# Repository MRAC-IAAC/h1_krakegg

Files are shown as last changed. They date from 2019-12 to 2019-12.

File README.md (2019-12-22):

# h1_krakegg

Krakegg is a soft robotics project exploring the implementation of bionic actuation for soft robotics grippers.

The repository contains the files, code & hardware components used in the project.

In the documents, you will find:

**A. Text instructions:**

0.Concept & process: explaining the overall process leading to the development of the final prototype for the soft robotics gripper.

0_01: Bill of materials: a list of the materials used for the production of the final prototype, with affiliated links to similar products that can be purchased from Amazon/ local retailers.

0_02: Build process: documenting the steps taken in order to build the final prototype

**B. 3D printing files:**

Structure : Print files for the air chamber, exoskeleton, and connection to the robot

Moulds : Print file for the silicone moulds for the fingers and knuckle spacer

**C. Circuit:**

03_circuit: Circuit diagrams for the communication and control circuit

03_arduino: Arduino code for the air control circuit

**Prototype demonstration videos:**

    Egg picking demonstration: https://www.youtube.com/watch?v=kh5d-S89E1A&feature=youtu.be

    Force sensor test: https://www.youtube.com/watch?v=OoQZakSipXg&feature=emb_title

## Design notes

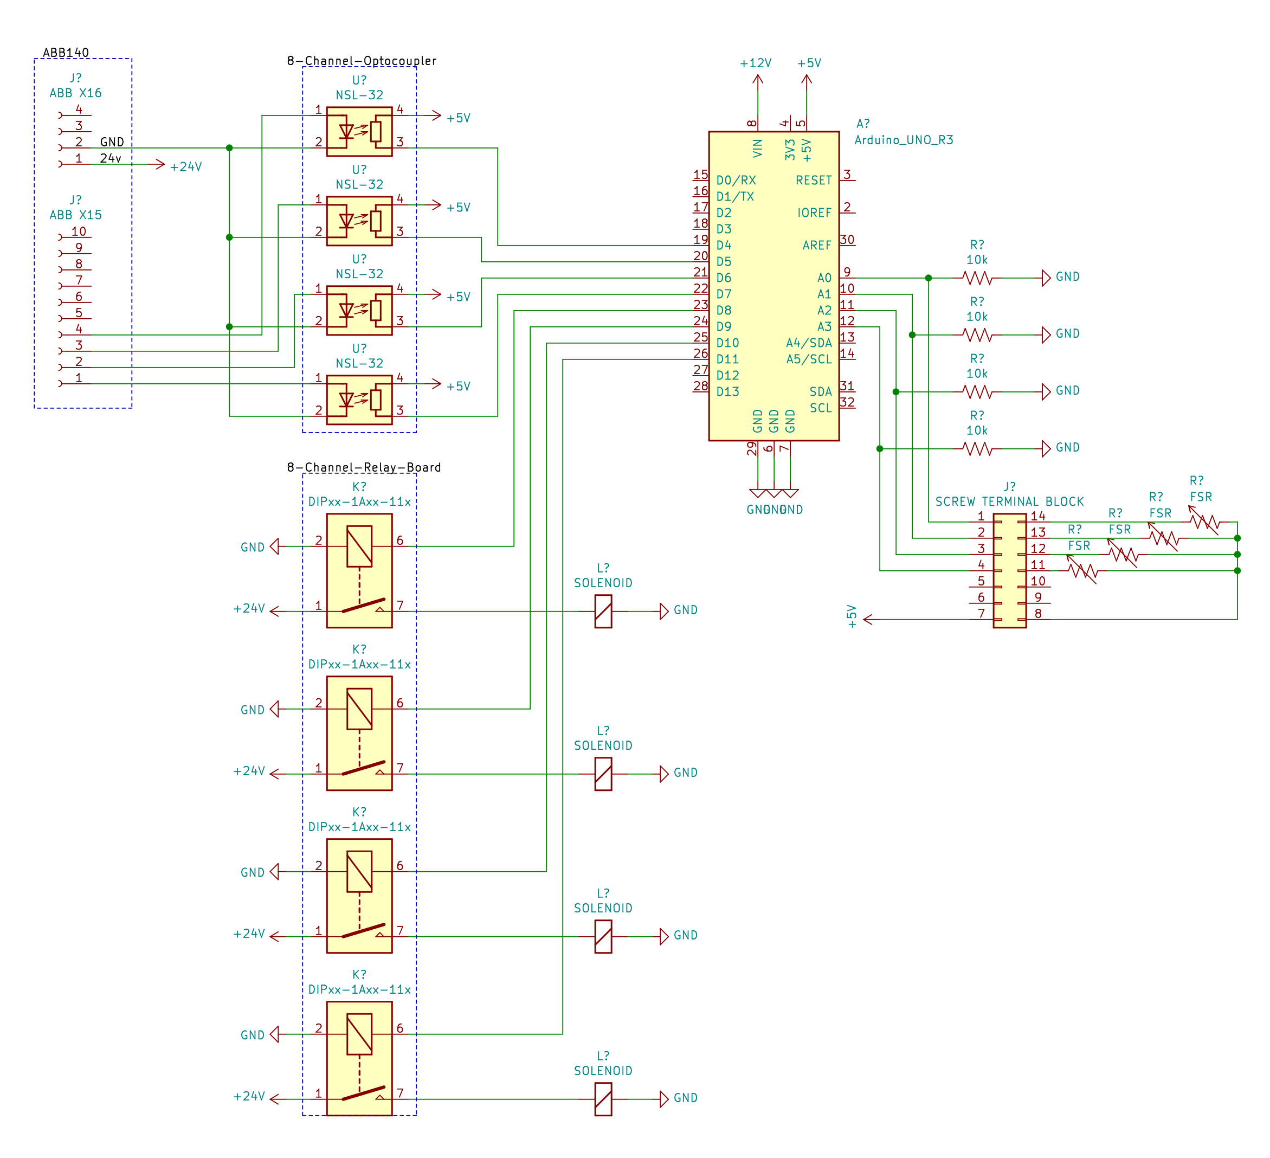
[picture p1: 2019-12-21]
images/soft-gripper-schematic.png

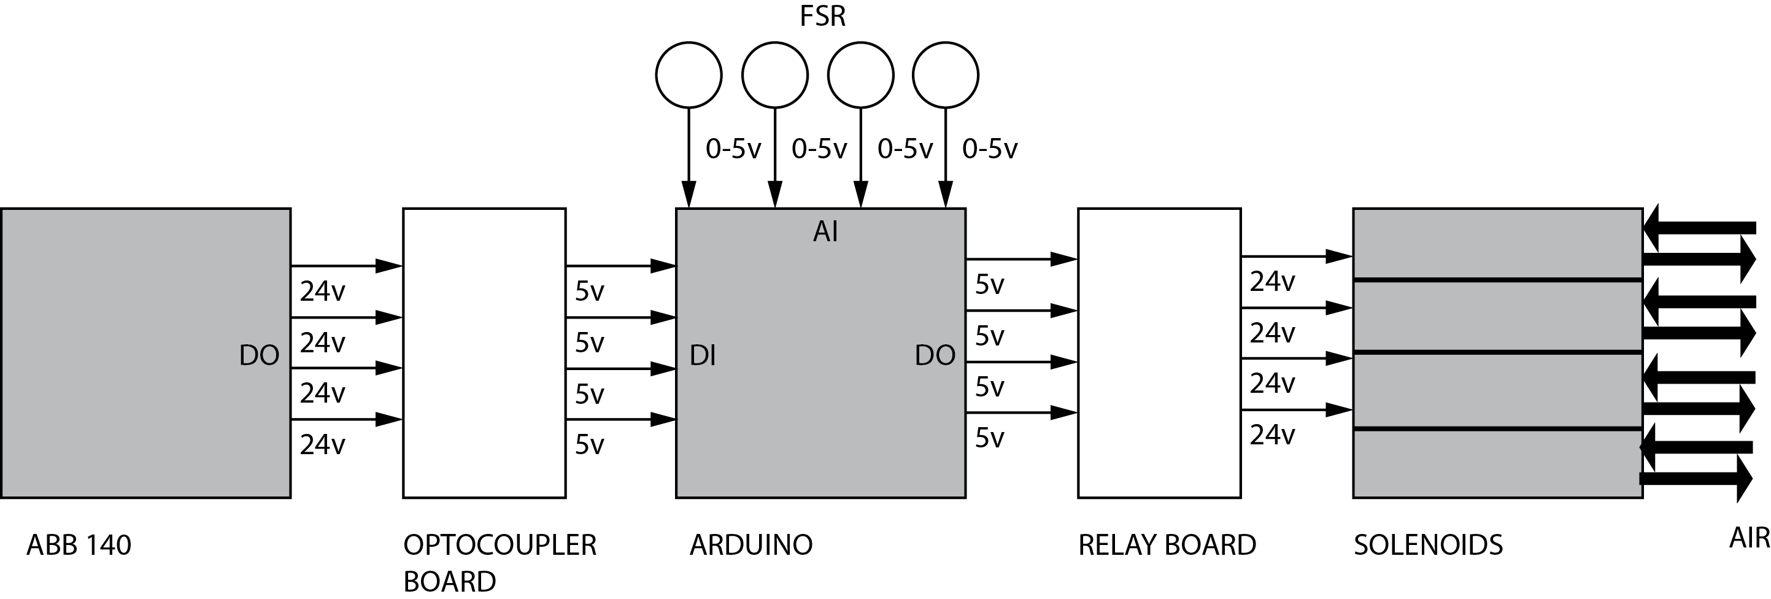
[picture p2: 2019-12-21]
images/gripper_board_diagram.png

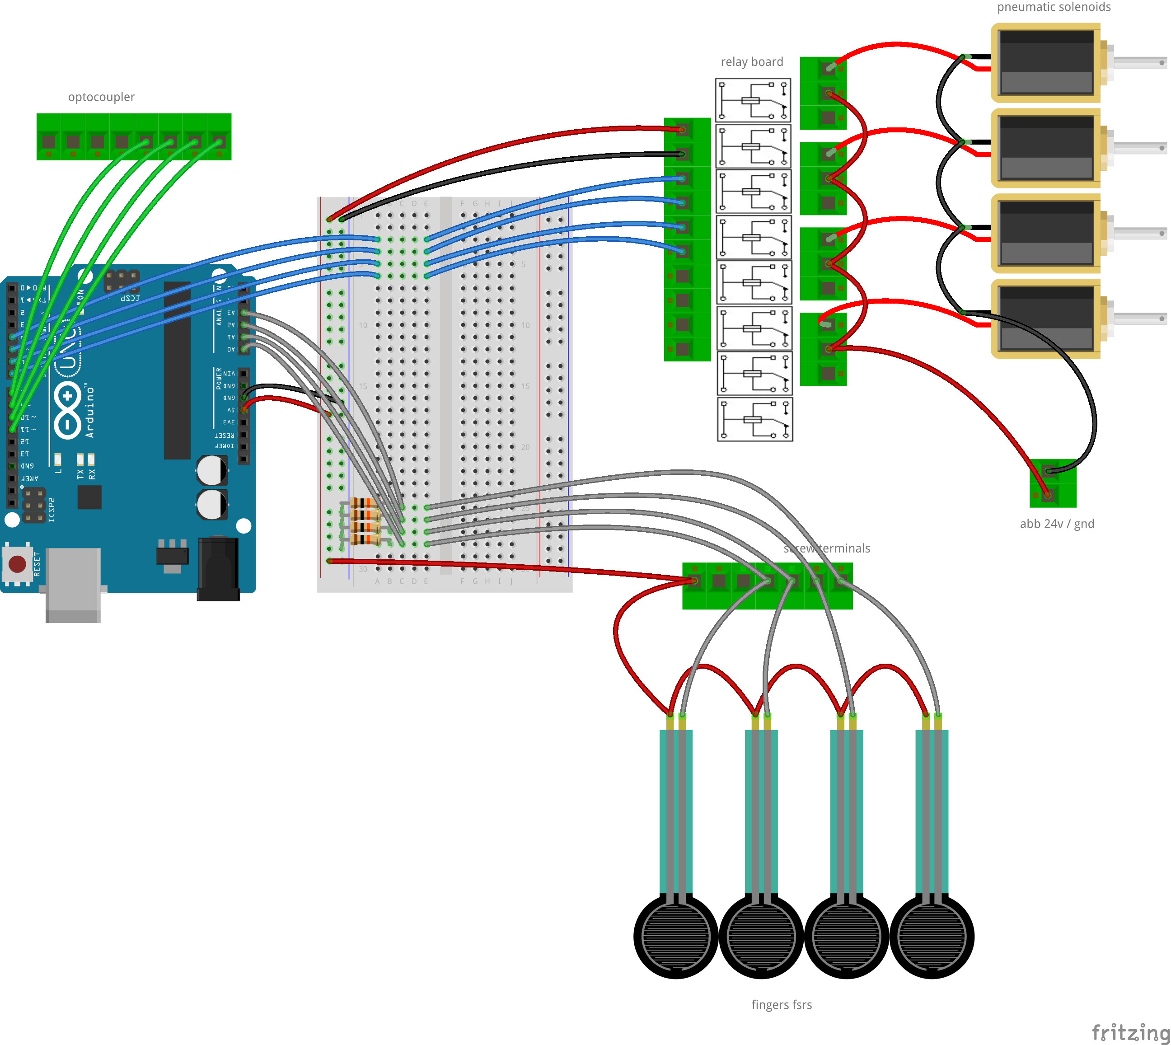
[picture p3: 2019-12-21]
images/soft_gripper_board_layout_bb.png

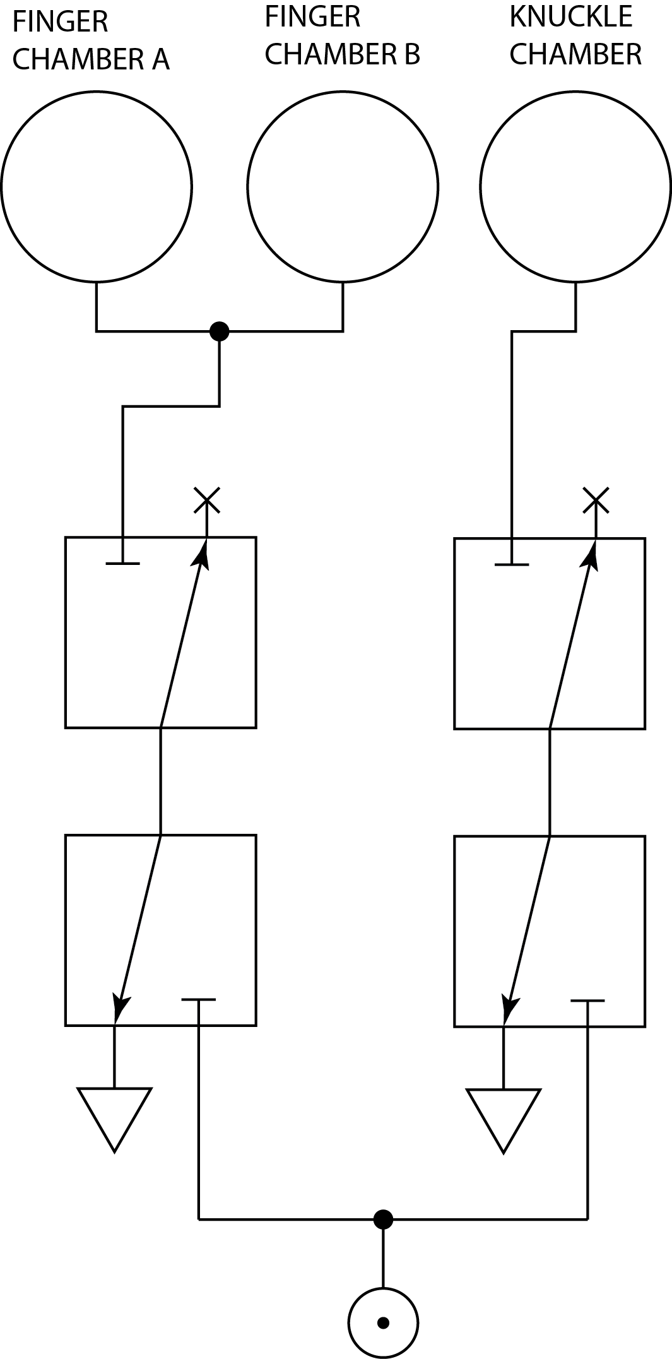
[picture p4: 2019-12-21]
images/pneumatic-diagram.png

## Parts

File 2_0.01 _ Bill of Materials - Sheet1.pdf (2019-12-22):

Bill of Materials

Printing and Casting
Item | Count | Purchase
PLA Printer Filament | 1 | https://www.amazon.com/OVERTURE-Filament-Consumables-Dimensional-Accuracy/dp/B07PGZNM34/
Casting Silicone | ~0.5 lbs | https://www.amazon.com/Smooth-Ecoflex-00-50-Platinum-Silicone/dp/B00GJ80HIC

Connections
Item | Count | Purchase
M3,M5 Bolts | | https://www.amazon.com/Hilitchi-510pcs-Stainless-Socket-Assortment/dp/B073SW4S6C
Pop Rivets | 4 | https://www.amazon.com/Tradespro-836341-Aluminum-Assortment-500-Piece/dp/B003L116P8

Electronics
Item | Count | Purchase
12v Power Supply | 1 | https://www.amazon.com/Switching-Universal-Regulated-Transformer-Computer/dp/B07C2WBR1L
Arduino Uno R3 Microcontroller | 1 | https://www.amazon.com/RoboGets-Compatible-ATmega328P-Microcontroller-Electronics/dp/B01N4LP86I
Optocoupler Board (4+ Channels) | 1 | https://www.amazon.com/24V-Optocoupler-Voltage-Level-Converter/dp/B06XKSFGXX
Relay Board (4+ Channels) | 1 | https://www.amazon.com/ELEGOO-Channel-Optocoupler-Arduino-Raspberry/dp/B01HCFJC0Y/
Force Sensitive Resistors | 4 | https://www.amazon.com/Sensitive-Resistor-Pressure-Diameter-Resistance-Type/dp/B07MP4RL9Q
Breadboard or Protoboard | 1 | https://www.amazon.es/Protoboard-contactos-Breadboard-prototipos-soldadura/dp/B00JGFDKBQ
10k Resistors | 4 | https://www.taydaelectronics.com/10-x-resistor-10k-ohm-1-4w-5-carbon-film-pkg-of-10.html
Mounting Plate or Project Box | 1
Jumper Cables and Wires | | https://www.amazon.com/Elegoo-EL-CP-004-Multicolored-Breadboard-arduino/dp/B01EV70C78
Screw Terminal Block (8 Positions) | 1 | https://www.amazon.com/a10073000ux0031-Position-Terminal-Covered-Barrier/dp/B00UWVYA30/

Pneumatics
Item | Count | Purchase
3 Way 2 Position 24 Pneumatic Solenoid | 4 | https://www.amazon.com/Position-Pneumatic-Electric-Solenoid-Valve/dp/B07YXSWZF4
Air Compressor | 1 | https://www.amazon.com/AstroAI-Portable-Compressor-Inflator-Protection/dp/B078LYX5YF
6mm Pneumatic Tubing | ~6m | https://www.amazon.com/uxcell-Pneumatic-Polyurethane-Meter-32-8ft/dp/B07859JVCY
6mm Pneumatic Push Connectors | 12 | https://www.amazon.com/Thread-Straight-Pneumatic-Fitting-Connectors/dp/B07BLRG8SH
6mm Pneumatic Splitter | 2 | https://www.amazon.com/Sydien-Connect-Pneumatic-Fittings-Splitter/dp/B07H14PVW2/

Tools
Item
Syringe
Soldering Iron
Wire STrippers
Tweezers
Screwdriver
Allen Wrenches
3d Printer

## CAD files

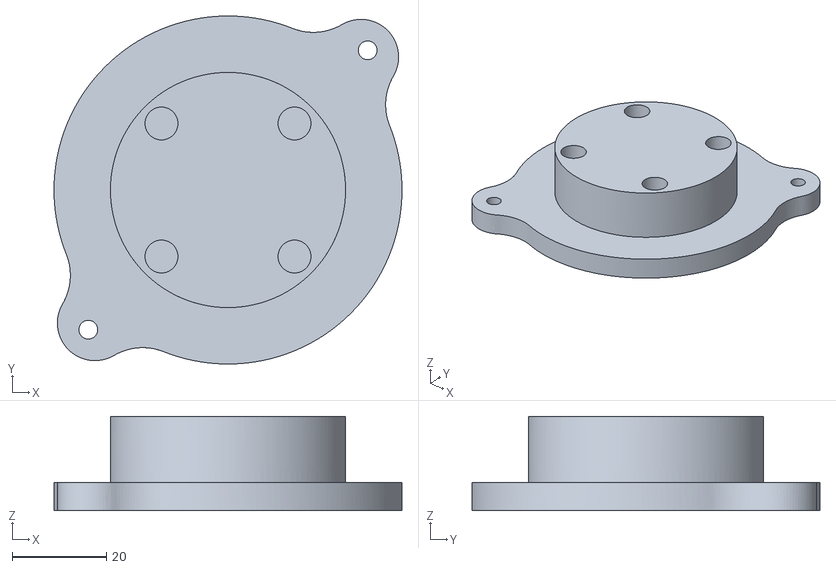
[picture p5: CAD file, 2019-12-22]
print_files/structure_connection_plane.stl
74.0 x 74.0 x 20.0

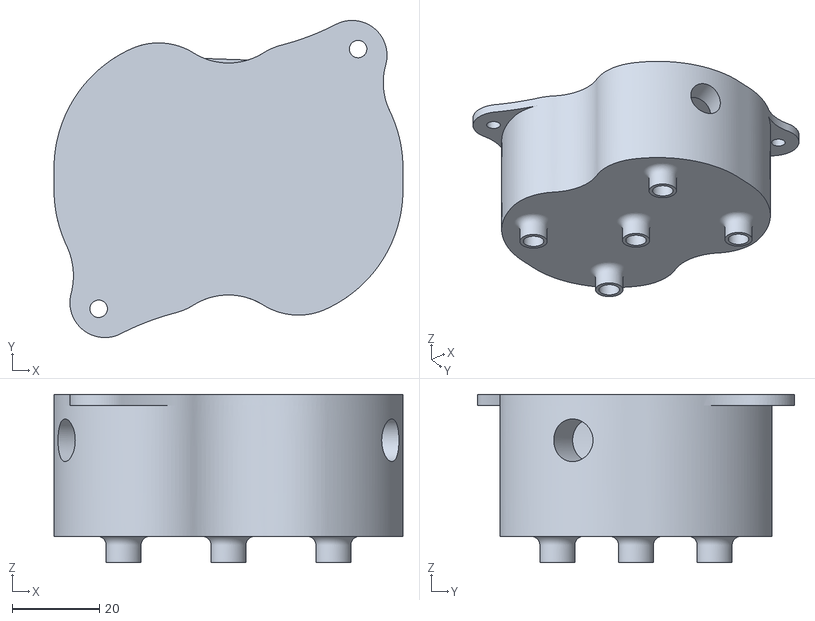
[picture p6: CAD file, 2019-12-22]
print_files/structure_air_chamber.stl
79.9 x 72.6 x 38.5

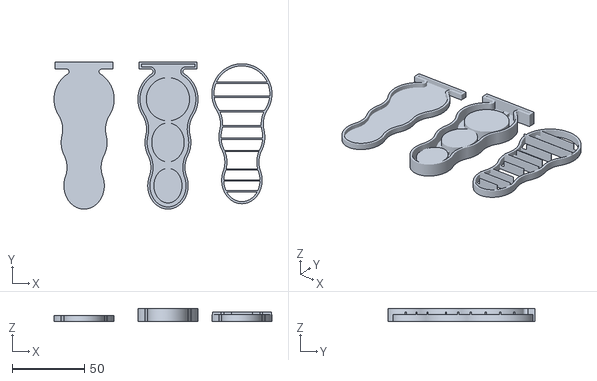
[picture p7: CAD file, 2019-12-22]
print_files/mould-fingers.stl
151.4 x 102.2 x 9.00

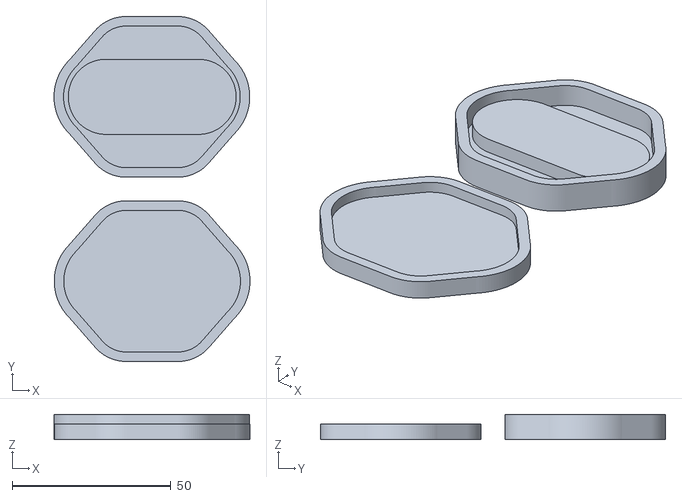
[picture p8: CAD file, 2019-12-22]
print_files/mould_knuckle_01.stl
61.7 x 108.7 x 8.00

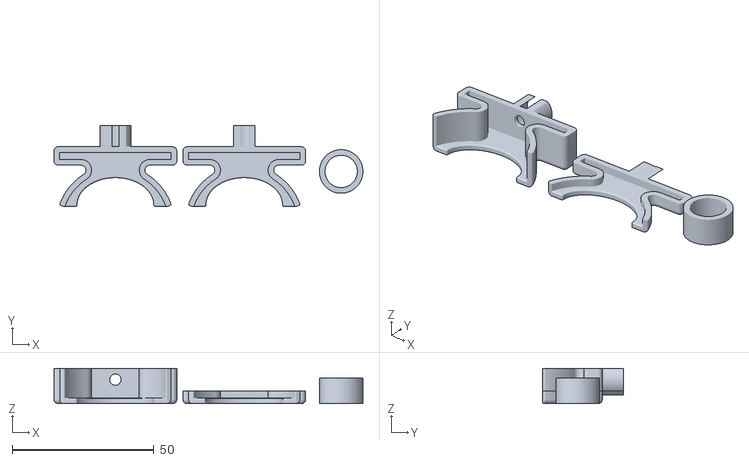
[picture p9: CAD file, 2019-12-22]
print_files/structure_exoskeleton.stl
109.0 x 28.6 x 12.5

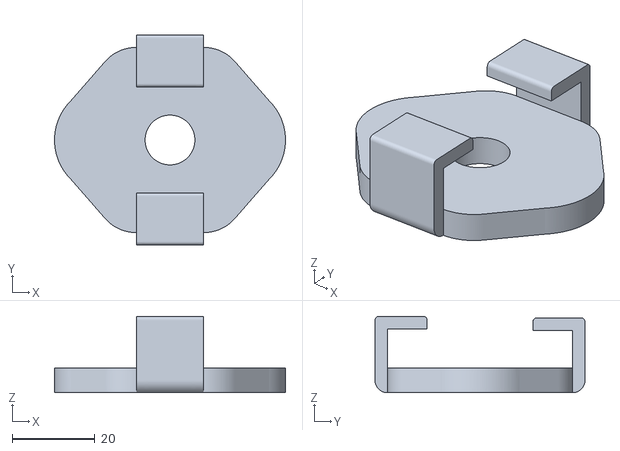
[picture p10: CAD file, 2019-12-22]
print_files/mould_knuckle_02.stl
55.7 x 50.6 x 18.4

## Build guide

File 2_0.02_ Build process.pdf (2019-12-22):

KRAKEGG / Stage 02 Final Prototype Build process

### 01. SOFT ROBOTICS FINGERS

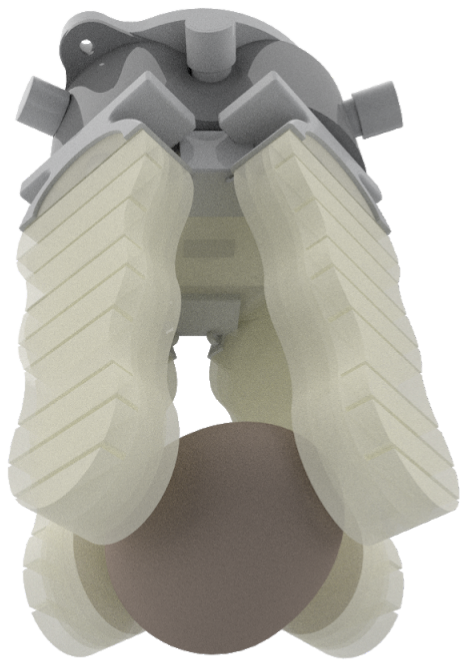
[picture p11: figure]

1. Design your mould using the attached grasshopper file, or download the 3D printing-ready files from the attached Rhino file.

Make sure to add a T-shaped end to the beginning of your air channel in order to later attach the fingers to the robot connection module.

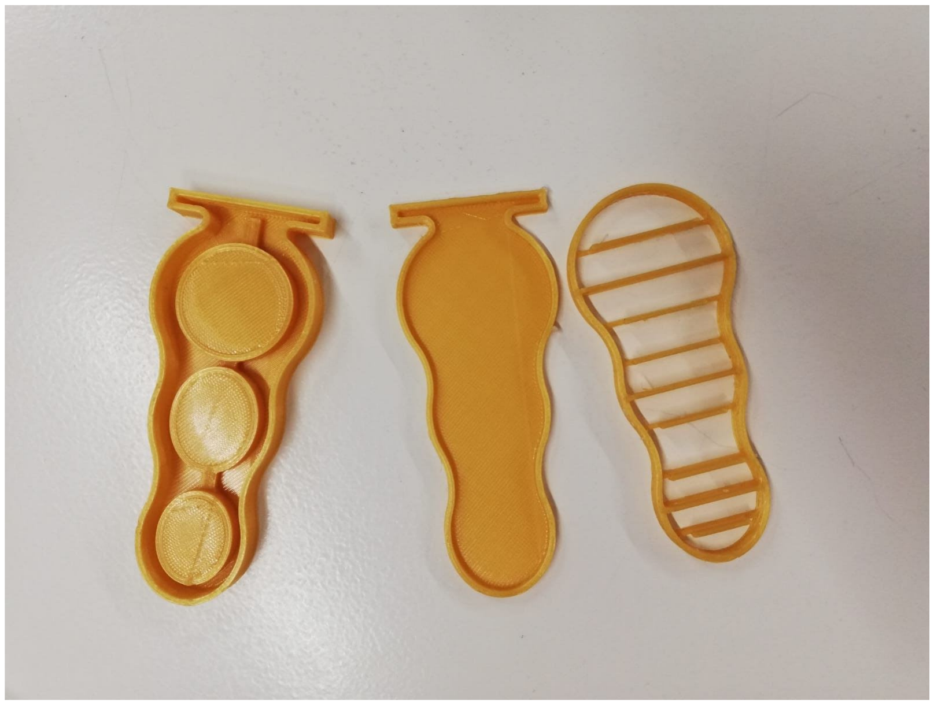
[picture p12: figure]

2. 3D print your mould (photo above)
3. Mix the two parts of Eco-flex 00-50 silicone according to the instructions on the packaging.
4. Pour the silicone in the bottom mould, up to the lip.
5. Pour the silicone in the main body mould, up to the lip. Then, place the spacer mould on top, making sure the indents are sunk in the silicone poured in the main body mould.

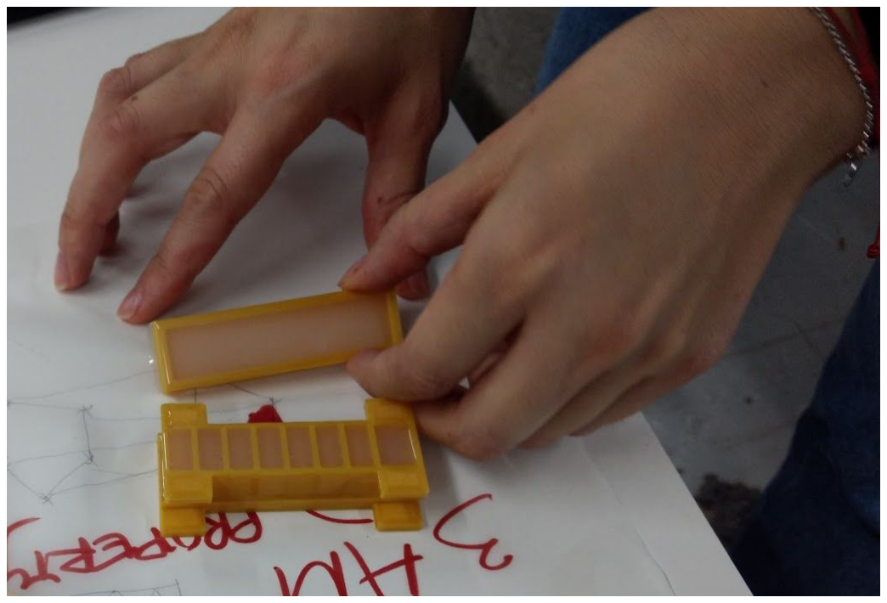
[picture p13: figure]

6. Leave the moulds to dry for at least 2 hours before carefully de-moulding.
7. Glue the bottom mould to the main body mould by applying a thin layer of silicone on the edges of the bottom mould and then placing the main body mould on top. Apply extra silicone on the vertical walls around the seam if needed to tightly close the mould.

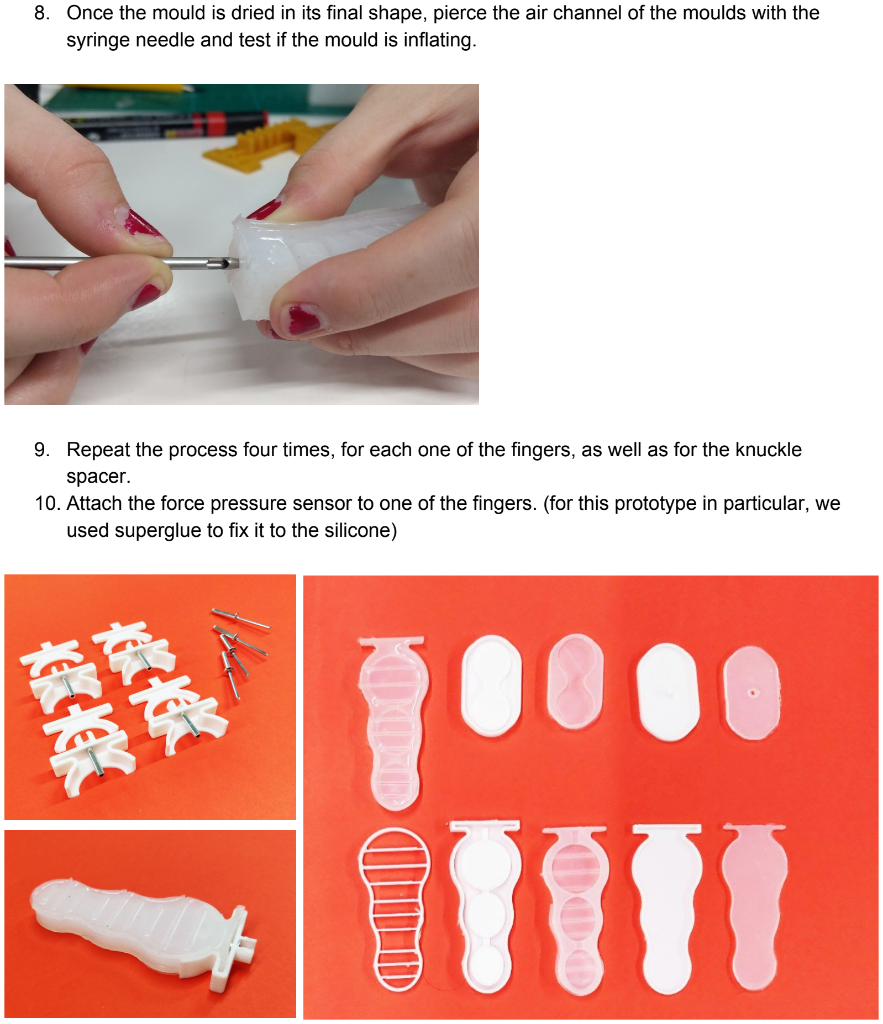
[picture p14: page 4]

8. Once the mould is dried in its final shape, pierce the air channel of the moulds with the syringe needle and test if the mould is inflating.
9. Repeat the process four times, for each one of the fingers, as well as for the knuckle spacer.
10. Attach the force pressure sensor to one of the fingers. (for this prototype in particular, we used superglue to fix it to the silicone)

### 02. CONNECTION TO ROBOTIC ARM

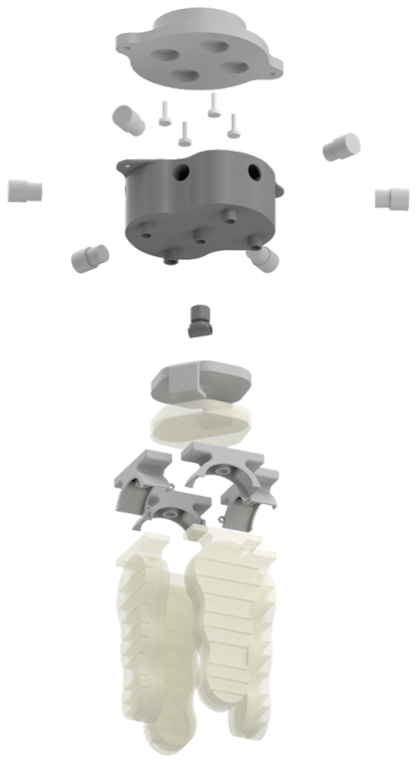
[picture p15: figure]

1. Download the Rhino file for the robot arm connection and 3D print it.
2. First screw in the robot arm connection plate using bolts compatible to the specific robot arm you are working with
3. Assemble the finger connections around the fingers
4. Attach the spacer connection plate to the silicone spacer and adhere it to the air chamber
5. Fix each finger connector in place on the air chamber using an adhesive
6. Attach the air chamber to the connection plate using the bolt tabs.
7. Insert the air connector into the air chamber using teflon tape

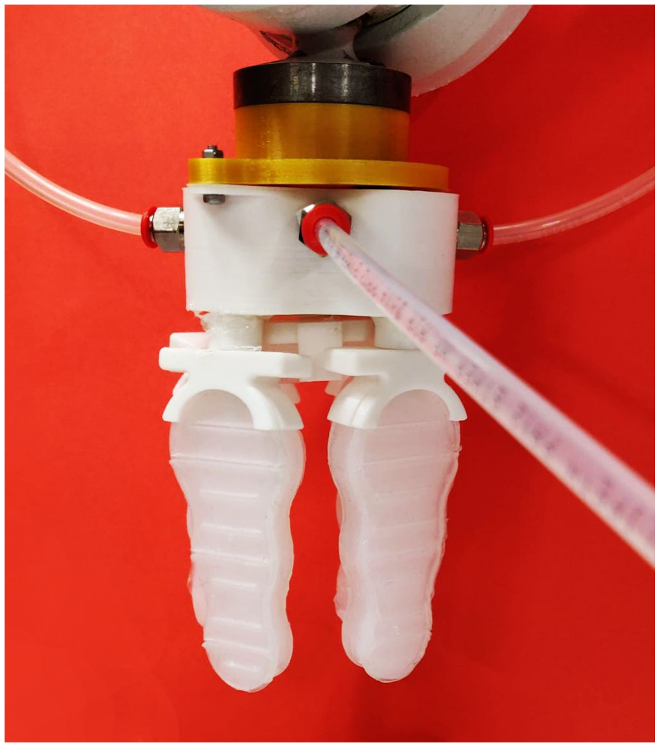
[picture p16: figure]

### 03. HARDWARE AND CONTROL SIGNALS

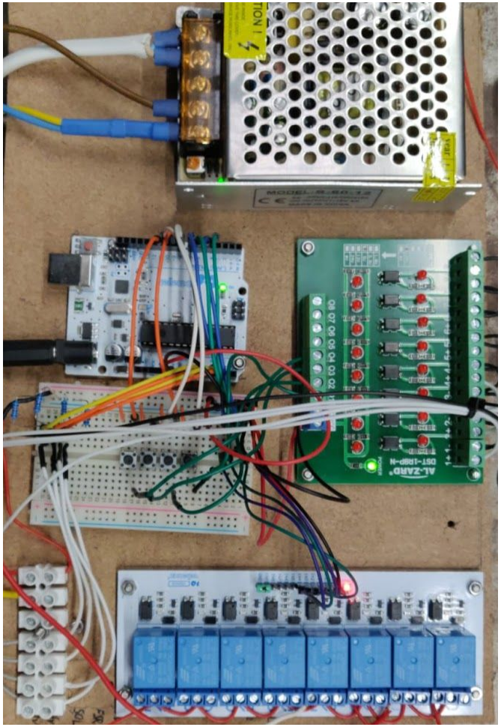
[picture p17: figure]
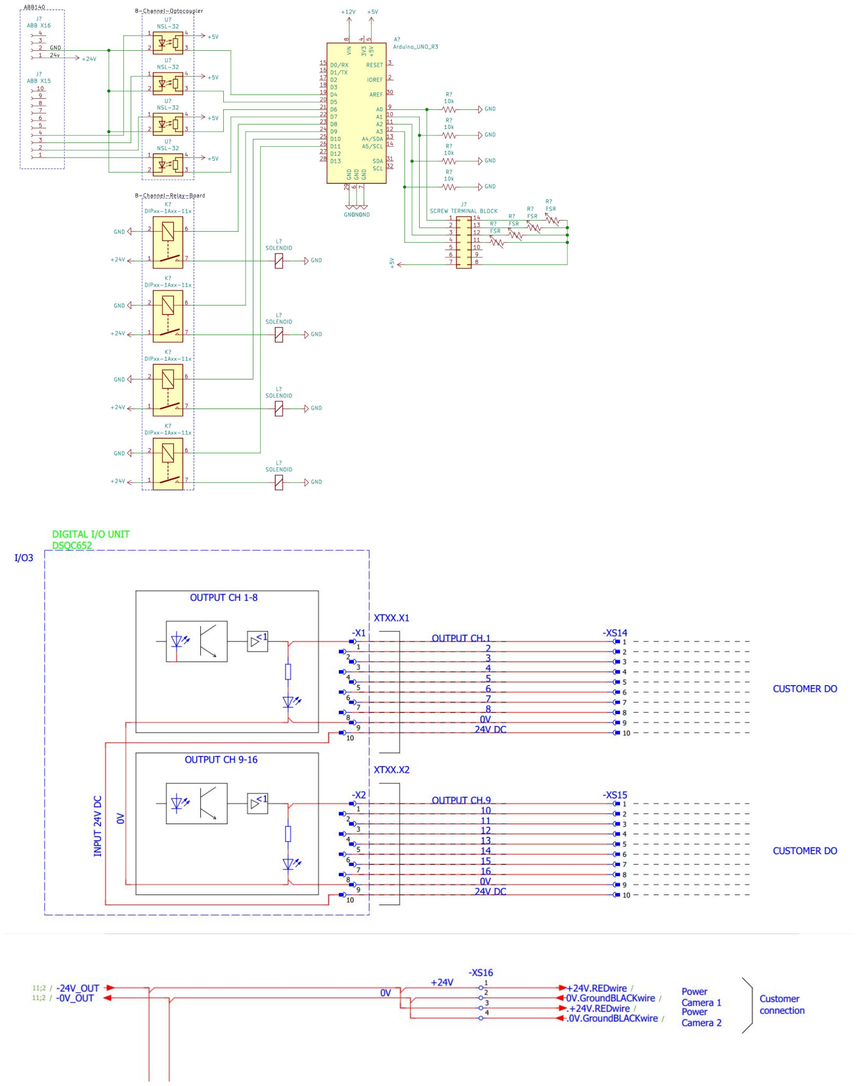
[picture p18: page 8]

1. First, the robot sends signals from its digital IO’s. This prototype used an ABB IR140, using the X15 and X16 ports for power and signals. (See diagram).
2. The 24v robot DO signal from X15 passes through an optocoupler to provide a 5v signal to the microcontroller. This lets the microcontroller know what state the program expects each air chamber to be in.
3. Each chamber (the fingers or the knuckles) can be in three states (either inflating, held, or deflating). Thus there are two signals (and two solenoids) running for each chamber. The first (closer to the air chamber) determines whether the chamber is currently held or is changing. The second determines the direction of change (either connected to the air supply to inflate or connected to open air to deflate).
4. However, the gripper still shouldn’t inflate continuously, so its state is also modulated by signals from force sensitive resistors on each of the fingers. These signals are combined with internal timers in the microcontroller to only inflate by controlled amounts.
5. The microcontroller output signal then passes through a relay which switches the 24v supply from X16 on the robot. This signal then connects to the air solenoids to supply or remove air to the gripper.

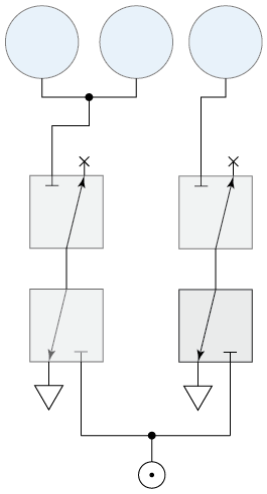
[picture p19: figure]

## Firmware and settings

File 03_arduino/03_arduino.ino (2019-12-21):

/**
   Robot Command State :
   - Inflate Fingers
   - Hold Fingers
   - Deflate Fingers
   - Inflate Knuckles
   - Hold Knuckles
   - Deflate Knuckles

   When finger line is high, inflate for time / until force. Hold when low. Leave open when second is high
   When knuckle line has rising edge, inflate for time
*/

#define PIN_FINGER_CHANGE           4
#define PIN_FINGER_DIRECTION        5
#define PIN_KNUCKLE_CHANGE          6
#define PIN_KNUCKLE_DIRECTION       7
#define PIN_FINGER_INFLATE_INPUT    8
#define PIN_FINGER_DEFLATE_INPUT    9
#define PIN_KNUCKLE_INFLATE_INPUT   10
#define PIN_KNUCKLE_DEFLATE_INPUT   11
#define PIN_LIGHT                   13
#define PIN_FSR_0                   A0
#define PIN_FSR_1                   A1
#define PIN_FSR_2                   A2
#define PIN_FSR_3                   A3

#define FINGER_INFLATE_TIME  200
#define KNUCKLE_INFLATE_TIME 200


#define FSR_CUTOFF           512

boolean fingerInflateSignal = false;
boolean fingerInflateSignalPrevious = false;
boolean fingerDeflateSignal = false;
boolean fingerDeflateSignalPrevious = false;

boolean knuckleInflateSignal = false;
boolean knuckleInflateSignalPrevious = false;
boolean knuckleDeflateSignal = false;
boolean knuckleDeflateSignalPrevious = false;

uint32_t fingerInflateTimer = 0;
uint32_t knuckleInflateTimer = 0;


void setup() {
  Serial.begin(9600);
  pinMode(PIN_FINGER_CHANGE, OUTPUT);
  pinMode(PIN_FINGER_DIRECTION, OUTPUT);
  pinMode(PIN_KNUCKLE_CHANGE, OUTPUT);
  pinMode(PIN_KNUCKLE_DIRECTION, OUTPUT);

  pinMode(PIN_FINGER_INFLATE_INPUT, INPUT);
  pinMode(PIN_FINGER_DEFLATE_INPUT, INPUT);
  pinMode(PIN_KNUCKLE_INFLATE_INPUT, INPUT);
  pinMode(PIN_KNUCKLE_DEFLATE_INPUT, INPUT);

  pinMode(PIN_LIGHT, OUTPUT);

  pinMode(PIN_FSR_0, INPUT);
  pinMode(PIN_FSR_1, INPUT);
  pinMode(PIN_FSR_2, INPUT);
  pinMode(PIN_FSR_3, INPUT);
}


void loop() {
  // Read Input Pins
  fingerInflateSignal = ! digitalRead(PIN_FINGER_INFLATE_INPUT);
  fingerDeflateSignal = ! digitalRead(PIN_FINGER_DEFLATE_INPUT);

  knuckleInflateSignal = ! digitalRead(PIN_KNUCKLE_INFLATE_INPUT);
  knuckleDeflateSignal = ! digitalRead(PIN_KNUCKLE_DEFLATE_INPUT);

  // Set up relay states
  boolean fingerInflateState = fingerInflateSignal;
  boolean fingerDeflateState = fingerDeflateSignal;
  boolean knuckleInflateState = fingerInflateSignal;
  boolean knuckleDeflateState = knuckleDeflateSignal;


//  // Finger Timing and State Control
//  if (fingerInflateSignal == true && fingerInflateSignalPrevious == false) {
//    fingerInflateTimer = millis();
//  }
//  if (fingerInflateSignal && fingerDeflateSignal == false && millis() - fingerInflateTimer < FINGER_INFLATE_TIME) {
//    fingerInflateState = true;
//  }

  float fsrValue0 = analogRead(PIN_FSR_0);
  float fsrValue1 = analogRead(PIN_FSR_1);
  float fsrValue2 = analogRead(PIN_FSR_2);
  float fsrValue3 = analogRead(PIN_FSR_3);
  if (fsrValue0 > FSR_CUTOFF || fsrValue1 > FSR_CUTOFF || fsrValue2 > FSR_CUTOFF || fsrValue3 > FSR_CUTOFF || fingerDeflateState) {
    fingerInflateState = false;
  }

//  // Knuckle Timing and State Control
//  if (knuckleInflateSignal == true && knuckleInflateSignalPrevious == false) {
//    knuckleInflateTimer = millis();
//  }
//  if (knuckleInflateSignal && knuckleDeflateSignal == false && millis() - knuckleInflateTimer < KNUCKLE_INFLATE_TIME) {
//    knuckleInflateState = true;
//  }
  knuckleDeflateState = knuckleDeflateSignal;

  // Write to relay outputs
  digitalWrite(PIN_FINGER_CHANGE, fingerInflateState || fingerDeflateState);
  digitalWrite(PIN_FINGER_DIRECTION, fingerInflateState);
  digitalWrite(PIN_KNUCKLE_CHANGE, knuckleInflateState || knuckleDeflateState);
  digitalWrite(PIN_KNUCKLE_DIRECTION, knuckleInflateState);

  // Update previous state variables
  fingerInflateSignalPrevious = fingerInflateSignal;
  fingerDeflateSignalPrevious = fingerDeflateSignal;
  knuckleInflateSignalPrevious = knuckleInflateSignal;
  knuckleDeflateSignalPrevious = knuckleDeflateSignal;
}

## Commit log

2019-12-22 renamed board
    [soft_gripper_board.kicad_pcb, soft_gripper_board.sch, soft_gripper_board_layout.fzz]
2019-12-22 added print files
    [mould-fingers.stl, mould_knuckle_01.stl, mould_knuckle_02.stl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]
